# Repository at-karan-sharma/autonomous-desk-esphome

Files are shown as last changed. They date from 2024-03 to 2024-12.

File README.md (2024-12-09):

# SmartDesk 2 Control for ESPHome

Seamlessly integrate your Autonomous SmartDesk 2 with Home Assistant, while still retaining keypad functionality.

<br/>
<p align="center">
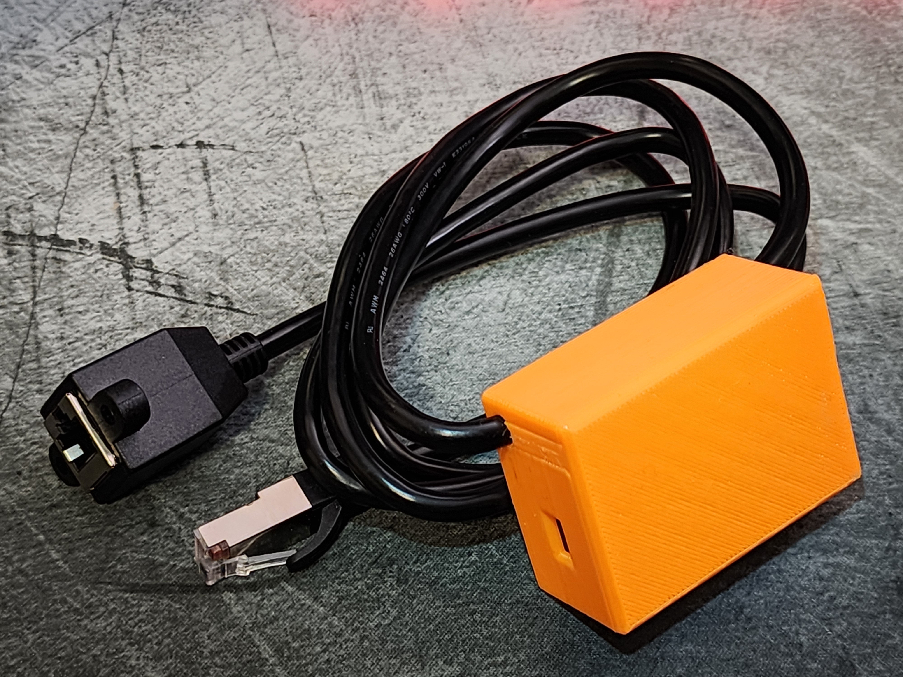
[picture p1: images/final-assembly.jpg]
Final assembly
  
</p>

## Features

- Incrementally move desk up/down using buttons on Home Assistant.
- Change desk height using a slider.
- Read height of desk in inches.
- Switch to one of four predefined height presets using a dropdown.
- Save the current desk height to one of the four memory presets, also with a dropdown.
<br/>
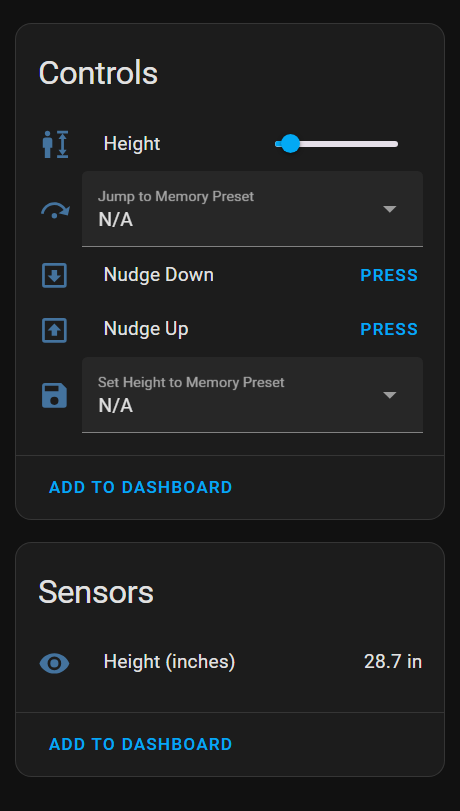
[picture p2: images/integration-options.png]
Integration options


## Credit

This project was built with reference and inspiration from [vipial1](https://github.com/vipial1/desky-ha), [developit](https://github.com/developit/desky), and [Stefichen5](https://github.com/Stefichen5/AutonomousControl). After failing to run the Espruino server on my ESP32, I adapted the communication logic for ESPHome. This had the benefit of making the Home Assistant integration trivial. I also added support for new features, like setting memory presets and reading the desk height in inches.

## Disclaimer

- It's your responsibility to ensure the desk doesn't collide with anything as it moves, which can cause injury or damage. Only use this integration when you are physically present to intervene.
  - Pressing UP/DOWN on the controller keypad should interrupt any command from this integration.
- Some low-voltage electronics work is needed. Use caution when using equipment like soldering irons and heat guns.

## Limitations

1. After pressing the UP/DOWN buttons on the keypad controller, certain integration features (moving to a user-defined height, memory preset save) fail until at least 30 seconds elapse.
2. Moving the desk to a user-defined height is functional but imperfect. E.g. suppose the desk is at height 80 (internal units, not inches), and you set the slider to 90 -- The desk will move up until the height is 90 +/- 3 and then slowly nudge up/down until it reaches 90 exactly. Compared to the smooth motion with presets, this is more janky.

## Getting started

### Hardware requirements

1. **ESP32 WROOM 3D development board**

2. **10P10C cable**:
   I used the 1.5M version of the [SinLoon RJ50 cable](https://www.amazon.ca/gp/product/B0B1ZKCRK4/)

4. **Soldering kit, wires (24 AWG) and wire stripper**

5. **1N4148 diode**:
   A 1N4148 diode is needed to continue using the keypad alongside the Home Assistant integration.

#### Optional but recommended:

1. **Heat-shrink tubes, electrical tape, hot glue**:
    For electrical insulation and for securing cable to housing

2. **Access to a 3D printer**:
   To print and use the included housing STL as in the project

### Electronics setup

1. Strip outer insulation of 10P10C cable.
   - If using provided 3D printable case, avoid stripping more than 35mm of insulation to allow for a secure fit.
2. Identify GND, RX, TX and 5V wires in the 10P10C cable. We will be tapping into these wires.
   - Refer to table below to find which PINs relate to which function.

  **Pin**   | **SinLoon RJ50** | **SmartDesk 2 cable** | **Function**
 -----------|------------------|-----------------------|--------------
  1         | Black            |                       |
  2         | Brown            |                       |
  3         | Red              |                       |
  4         | Orange           | Red                   | Sleep
  5         | Yellow           |                       |
  6         | Green            |                       |
  7         | Blue             | Orange                | GND
  8         | Purple           | Yellow                | RX
  9         | Gray             | Green                 | TX
  10        | White            | Blue                  | 5V

   - Check if your cable's pin color layout matches the layout for the SinLoon RJ50 cable. If so, simply use its layout to identify the relevant colors.
  <br/>
  <p align="center">
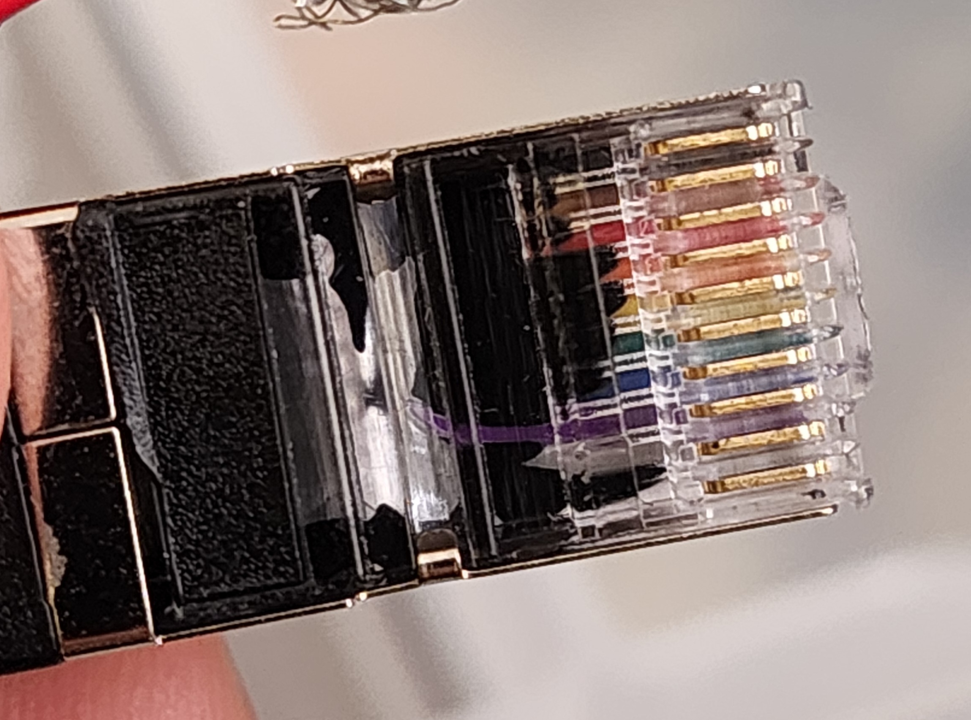
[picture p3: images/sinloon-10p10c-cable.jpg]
My SinLoon RJ50 cable as a reference
    
  </p>

3. Strip insulation off the 4 relevant inner wires and solder wires to them, making 3-way taps.
4. (Highly recommended) Create breadboard prototype with cable attached to ESP32 to verify the whole system works. Jump ahead to [ESPHome](#esphome-setup) and [Home Assistant](#home-assistant-setup) sections for testing.
   - Pin 16 (RX) of ESP32 is connected by green wire to tapped wire for RX.
   - Pin 17 (TX) is connected by purple wire to the 1N4148 diode, with the darker end (cathode) pointed towards the ESP32 side. Other end of diode connects to TX wire.
   <br/>
   <p align="center">
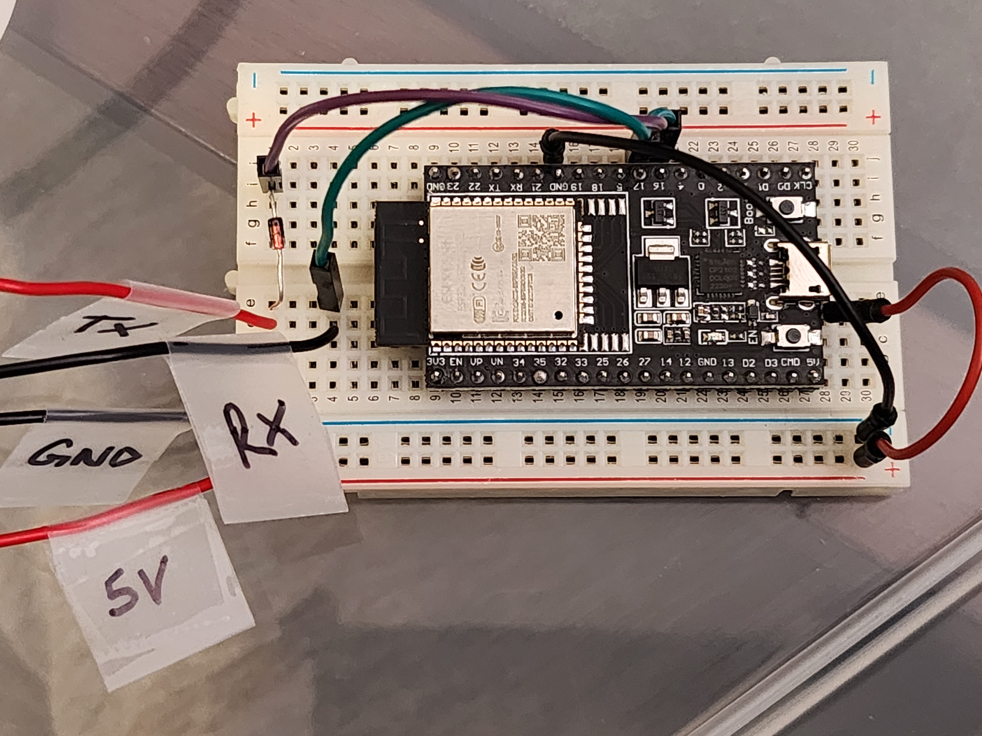
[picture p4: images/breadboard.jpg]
Breadboard layout
     
   </p>
   - I labelled the wire ends with their respective functions because I only had red/black wires on hand :/
5. Add shrink tubes before soldering the parts and wires to the top of the ESP32 board.
   <br/>
   <p align="center">
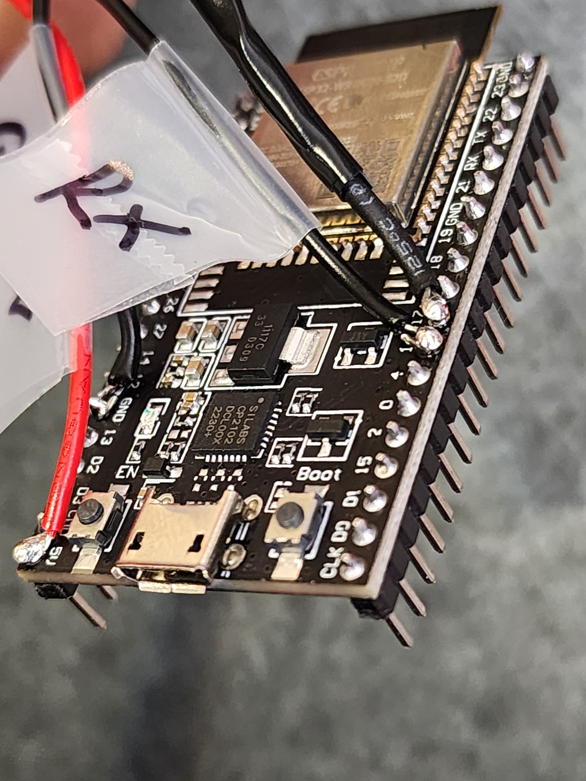
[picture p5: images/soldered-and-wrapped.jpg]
Soldered and wrapped wiring
     
   </p>
6. (Optional) Print 3D casing using the included files and assemble.
   - When assembling, use a ziptie on either end of the stripped section, before fitting it into the case with hot glue. This will help prevent the cable from getting yanked out of the case.

  <br/>
  <p align="center">
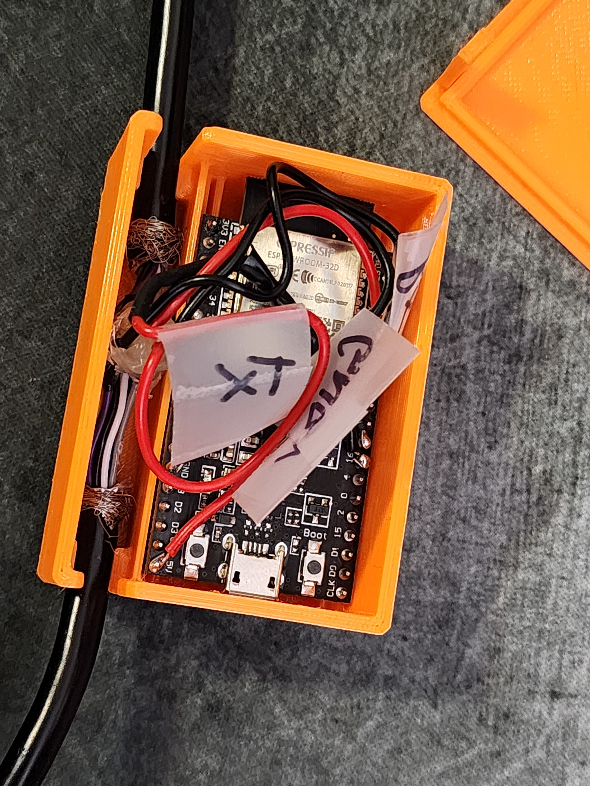
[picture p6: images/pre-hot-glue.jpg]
Before applying hot glue
    
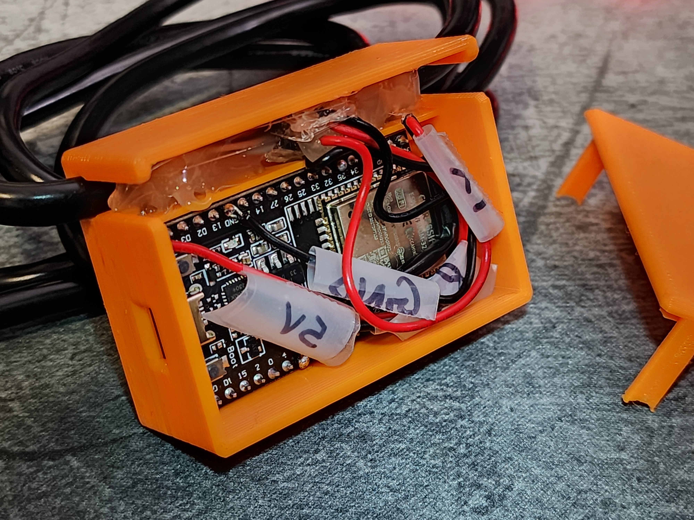
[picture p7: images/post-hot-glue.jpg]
After applying hot glue
    
  </p>

### ESPHome setup

1. Create a new device in ESPHome dashboard, and configure name, static ip address etc, as needed.
2. Set the remote package and substitutions by adding the following snippet. Refer to example.yml for more info.
   - Note: the min/max height is based on the extended model of the SmartDesk 2. If you have the regular model, the range is probably 75-123 based on [this gist](https://gist.github.com/developit/d610e45a522810b5287db61e554ae9c9).
  ```yaml
  packages:
    Autonomous_Desk: github://at-karan-sharma/autonomous-desk-esphome/config/desky.yml@main

  substitutions:
    uart_tx_pin: "17"
    uart_rx_pin: "16"
    desk_min_height: "66"
    desk_max_height: "131"
  ```
3. Install config to the ESP32 over wireless/serial connection.

### Home Assistant setup

1. Look for the new ESPHome device in Home Assistant > Settings > "Devices & services" under the "Discovered" section.
2. Click on "Configure" and add the encryption key (if configured in ESPHome) to finalize setup.

## Contribution

Feel free to contribute to this project by submitting issues or pull requests. Feedback and suggestions are also welcomed.

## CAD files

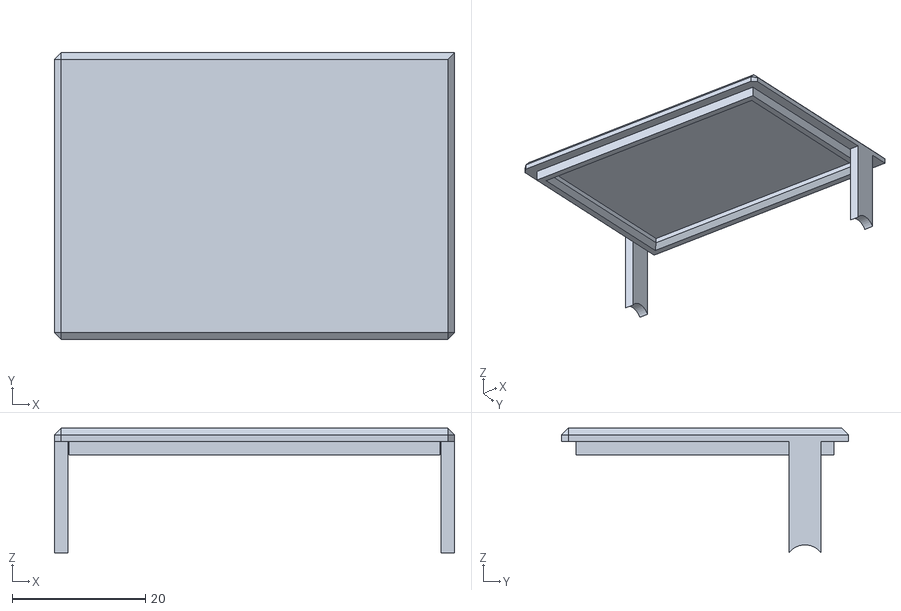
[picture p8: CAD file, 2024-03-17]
3d-printable-case/desky-esp32-cover.stl
60.0 x 43.0 x 18.7

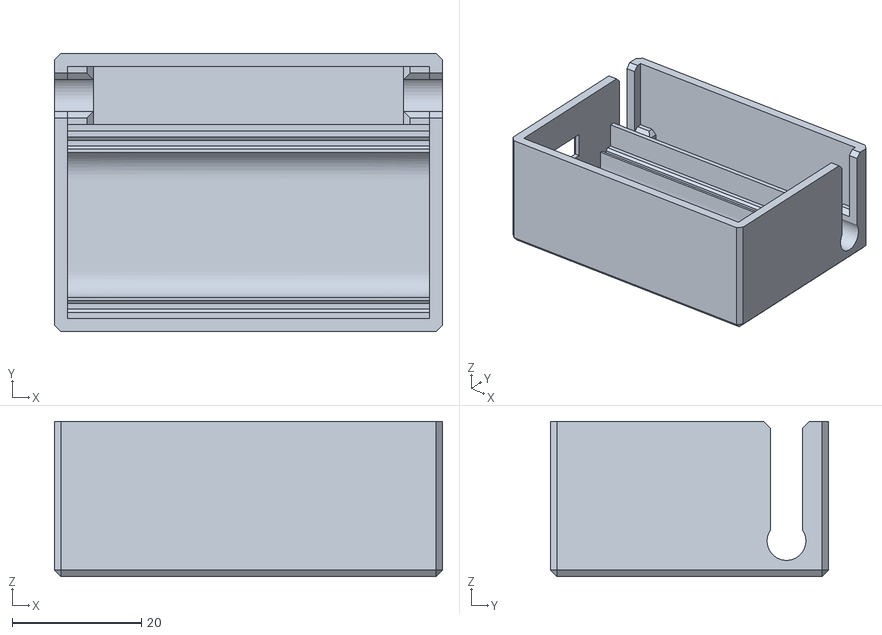
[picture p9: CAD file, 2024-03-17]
3d-printable-case/desky-esp32-base.stl
60.0 x 43.0 x 24.0

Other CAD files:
3d-printable-case/desky-esp32-box v5.f3d

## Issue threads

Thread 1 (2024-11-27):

Troubleshooting help

OwlTrkr, 2024-11-27:
I love that I found this as I have been wanting to smarten up my SmartDesk for a while.  I'm new to arduinos, so I'm not sure where to go next.  I got some WROOM 32 (not D) on sale off Amazon.  From what I can find it just has slightly less performance than the 32D.  Same wire pinouts, but paid attention to the labels and should have mine on the right pins.  It will power up off the desk power, connects to HomeAssistant and shows the config, original remote is working on passthrough, but the ESP is not sending/receiving to the desk.  Height readout doesn't update and change commands don't respond.

OwlTrkr, 2024-11-27:
Thanks for the swift reply.
1. The 10p10c cable I got, https://www.amazon.com/dp/B0B1ZKCRK4, was identical.
2. I cut the cable in half to save length, and connected only the important wires.  So the taps have to be right for that part for the original remote to still work.
3. I could probably swap the 16 and 17 in the config to test swapping the RX and TX too?
4. On thinking the diode might actually be the problem.  It is oriented dark end toward the ESP, but I put shrink tubing over it before thinking.  I might have torched the poor thing.

OwlTrkr, 2024-11-27:
Ha! Two things that fixed it that I probably just needed to sleep.  Swapping the diode was probably a good idea, the other was that I think the first version of the YAML I sent had the wrong TX/RX pins assigned, and it wouldn't install new ones over wifi.  Had to plug it in to update.  It works!!

OwlTrkr, 2024-11-27:
OK, new one now that I have it working.  When the "Jump To Memory Preset" is selected for a height and the desk starts moving, the selection returns to N/A after a moment, and the desk stops prematurely, as though another button was pressed that cancels the move.

OwlTrkr, 2024-11-27:
Working kludge in place.  I forked and increased that 2s delay to 15s, to cover the longest distance my presets have.  Works perfectly!

at-karan-sharma, 2024-11-28:
Glad you got it working :)

It does indeed sound like a movement detection issue. If you have time, feel free to add [debug statements](https://esphome.io/components/logger.html) to confirm if `desk_moving` is still false after 2s.

Increasing the delay should fix it, but ideally, we'd minimize the constant duration for which NOOPs are emitted. E.g. with a 15s delay: suppose you jump between 2 nearby height presets in 5s, the integration will continue sending NOOPs for 10 more seconds, which could interfere with keypad commands.

Closed 2024-11-27.

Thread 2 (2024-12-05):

Tapping in won't work

BedirT, 2024-12-05:
Hi,

Thanks for the documentation and the code. But i am confused about your wiring. I have tried setting up exactly as described but i can't seem to get it working properly.

I have an ESP32-WROOM (I also tried it with an ESP8266 but couldn't handle that as well). The only difference i can see is that i am tapping into the cable instead of using a separate UART cable. But i cannot see why that would cause any issues. Couple things that seems to be not working for me:
1. If i don't wake up the desk with the keypad, i get no reaction from it with ESP.
2. Even when i get some reaction after the wake up it is super jagged and buggy and barely moves at all.
3. I tried to make sure cabling is the same as the pic, and tried a bunch of other ways as well.

If you could help i would appreciate it!

at-karan-sharma, 2024-12-05:
Hi @BedirT,

Thanks for giving this project a try! I wondered whether it was feasible to tap the cable between the keypad and motor controller directly, so it's cool that you're testing this approach. Should be possible I feel.

Points 1 and 2 make me wonder if the ESP32 is getting enough (or too much) power. Some ideas:
1. Can you use a multimeter to confirm the voltage between the 5V tap and the GND tap is indeed 5 volts?
2. When you wake up the desk with the keypad, does the voltage remain at 5V?
3. How did you join the tapping wire to the cable? If you soldered them, is the connection solid (i.e. no cold joints)?
4. If you take out the ESP32 and power it only via USB, is it otherwise stable?

BedirT, 2024-12-05:
Thanks for the quick reply!

1. Yes, I get 5V for this.
2. Yes the voltage is stable at 5V still.
3. I am using wago type connectors.
4. Do you mean using only the keypad? If so yes it works just as it did before when i remove the esp connections. To be clear even when I use with the ESP the keypad works just fine as intended.

at-karan-sharma, 2024-12-06:
Hmm wago connectors should be pretty stable, assuming the wires are the right gauge. About point 4, I meant to ask if the ESP32 works reliably with esphome. We can rule out any hardware issues if you try a simple config like blinking an LED while the ESP32 is powered over USB (versus powered by the tapped wires).

Do the colors of the tapped wires line up with this table from [Stefichen5](https://github.com/Stefichen5/AutonomousControl)?
| color  | function |
| ------ | -------- |
| red    | sleep(?) |
| orange | GND      |
| green  | TX       |
| yellow | RX       |
| blue   | 5V       |

A pic of the ESP32 board and the tapped wires would be helpful also in understanding your setup.

Worst case, depending on your comfort level, you can try a logic analyzer to confirm the signals being sent across the wire, like Stefichen5.

BedirT, 2024-12-06:
Yeah the ESP works with no issues. I tested the board couple times.

The colors match exactly. It is also marked in the keypad.

What do you mean by right gauge? I am using some jumper wires, which i think are 28 Gauge. Do you think that could cause enough interference to distrupt the signal? They are pretty short so i thought that couldn't cause the issue? If you think thats okay ill send the image, if not i can try with lower gauge to see if it works and send a pic if not.

at-karan-sharma, 2024-12-07:
The gauge being an issue is a long shot for sure, but worth ruling out.

Going back to your point 1, is the ESP offline in the ESPHome dashboard until you interact with the keypad? If you're able to see live logs from the ESP, you can check the raw UART data sent across the wire:
1. Replace the snippet from the README with the contents of `config/desky.yml`.
2. Uncomment this line `// UARTDebug::log_hex(direction, bytes, ':');`
3. Save/Install config and view logs. You should see hex data getting regularly printed every second.

If instead no data is printed until you interact with the keypad, I can only conclude it is an electronics issue.

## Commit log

2024-03-17 Add project files
    [desky-esp32-base.stl, desky-esp32-box v5.f3d, desky-esp32-cover.stl]
2024-12-09 Fix motion detection logic
    - Use a delayed_off filter to determine when desk has stopped instead of
    manually calculating it from the number of motionless iterations
    - Improve robustness of custom height setting and preset
    setting/jumping. When desk is in motion, or preset setting is
    taking place, other user actions are gracefully blocked.
    - Stop custom height actions after 2-3 seconds after desk height does
    not change for that duration. Previously, if users clicked a keypad
    button and then set a custom height via the integration, the desk
    would get stuck in a loop of turning the motors on/off until 30s
    elapsed.
